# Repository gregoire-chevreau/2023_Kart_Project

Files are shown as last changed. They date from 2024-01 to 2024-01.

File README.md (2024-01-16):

# 2023_Kart_Project

Dans ce dossier GitHub, vous trouverez toutes les informations pour continuer le projet.
Ce dernier est composé d'une carte de commande avec la NUCLEO STM32G431RB ainsi que d'un onduleur.

## Table des matières

- [Cahier des charges](#charges)
- [PCB de commande](#commande)
- [Onduleur](#onduleur)
- [Code](#code)

## Cahier des charges

Le but est de faire rouler le kart à 20 km/h.
Le moteur est un moteur OZO 3500W à alimenter en 72 V (https://ozo-electric.com/fr/moteurs-centraux-brushless/679130-moteur-moto-3500w-electrique-central-brushless-bldc.html).
La batterie fourni une tension de  72V (https://ozo-electric.com/fr/72v/282892-batterie-72v-21ah-1512wh-pvc-panasonic-lithium.html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).

## PCB de commande

Ce PCB est composé de la carte NUCLEO, d'une isolation galvanique et d'un level-shifter.
L'isolation galvanique pourra disparaître pour faire un seul PCB commun par la suite. En effet, des optocoupleurs sont prévus comme driver de MOSFET.

## Onduleur

L'onduleur a les caractéristiques suivantes : 
- Tension d'alimentation : 72 V
- Courant nominal : 48 A
De plus, sur cette carte, nous avons prévu une alimentation 15V afin d'alimenter la carte de commande.

## Code

Le code est réalisé avec STM32CubeIDE.
Nous utilisons : 
- 6 sorties GPIO pour commander l’onduleur
- 3 entrées GPIO pour les capteurs Hall
- 1 entrée ADC pour le potentiomètre
- 1 entrée ADC pour le capteur de tension de la batterie
- 1 entrée ADC pour les capteurs de courant de phase

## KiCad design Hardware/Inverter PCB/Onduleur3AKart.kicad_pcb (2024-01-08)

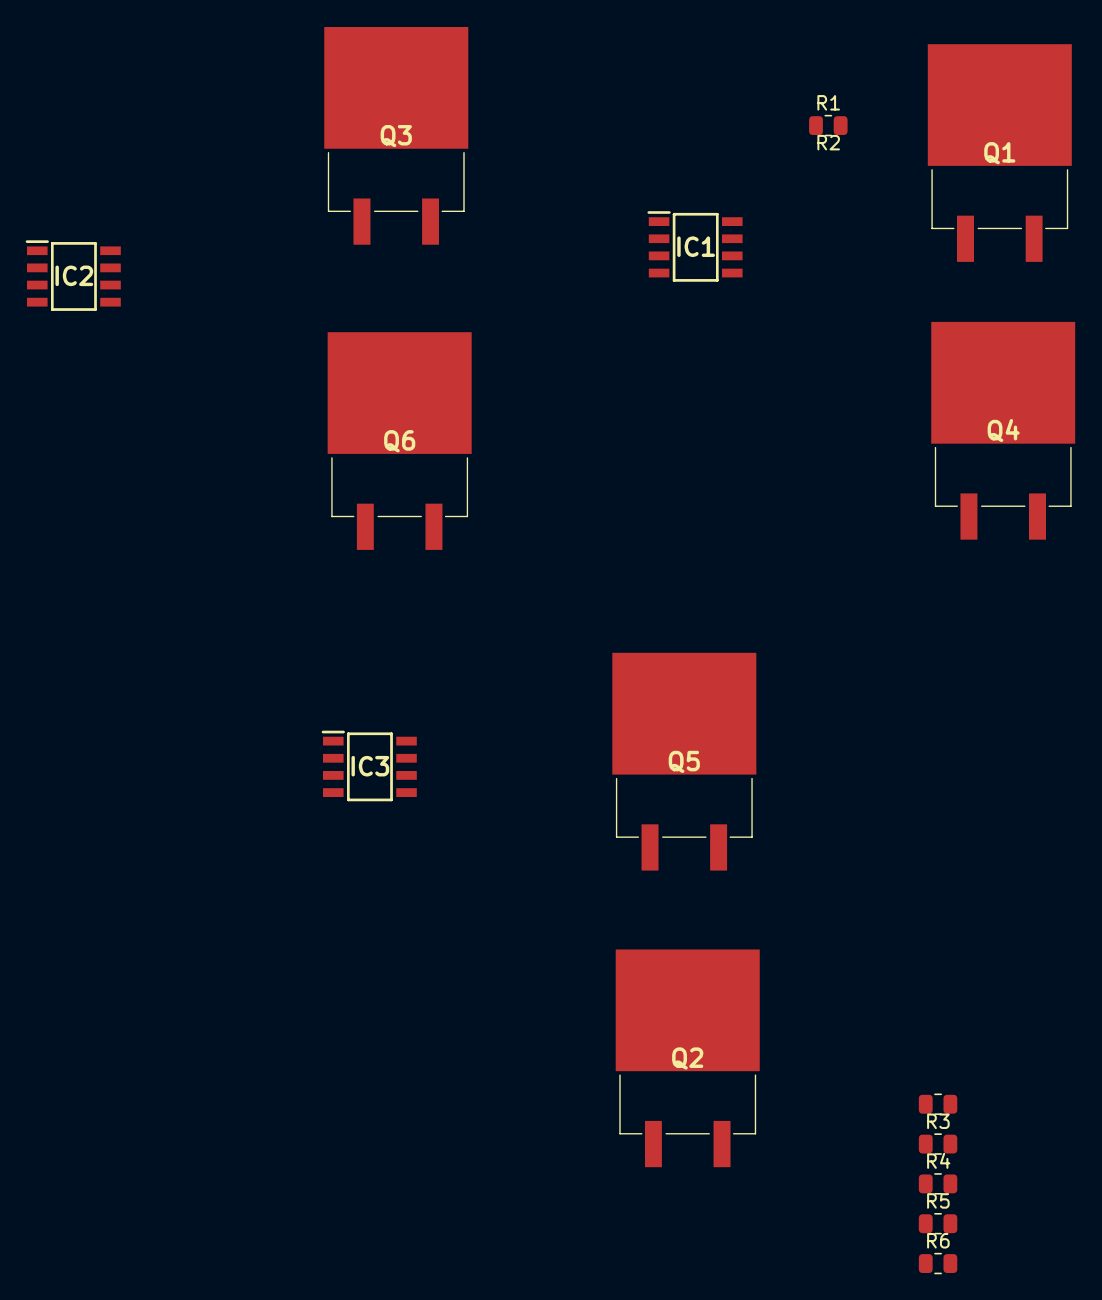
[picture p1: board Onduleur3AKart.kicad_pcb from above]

Board: 2 copper layers, 15 parts (0 on the bottom side), 15 nets, no tracks yet.

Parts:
IC1, IC2, IC3: TPS2836DR
Q1, Q2, Q3, Q4, Q5, Q6: SUM60N10-17-E3; SUM60N1017E3
R1, R3, R5: 1; R_0805_2012Metric
R2, R4, R6: 5; R_0805_2012Metric

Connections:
unnamed: IC1.6 (BOOTLO), R2.1
unnamed: IC1.7 (HIGHDR), R1.1
unnamed: IC2.6 (BOOTLO), R4.1
unnamed: IC2.7 (HIGHDR), R3.1
unnamed: IC3.6 (BOOTLO), R6.1
unnamed: IC3.7 (HIGHDR), R5.1
unnamed: Q1.1 (G), R1.2
unnamed: Q1.3 (S), Q4.2 (D)
unnamed: Q2.1 (G), R3.2
unnamed: Q2.3 (S), Q5.2 (D)
unnamed: Q3.1 (G), R5.2
unnamed: Q3.3 (S), Q6.2 (D)
unnamed: Q4.1 (G), R2.2
unnamed: Q5.1 (G), R4.2
unnamed: Q6.1 (G), R6.2

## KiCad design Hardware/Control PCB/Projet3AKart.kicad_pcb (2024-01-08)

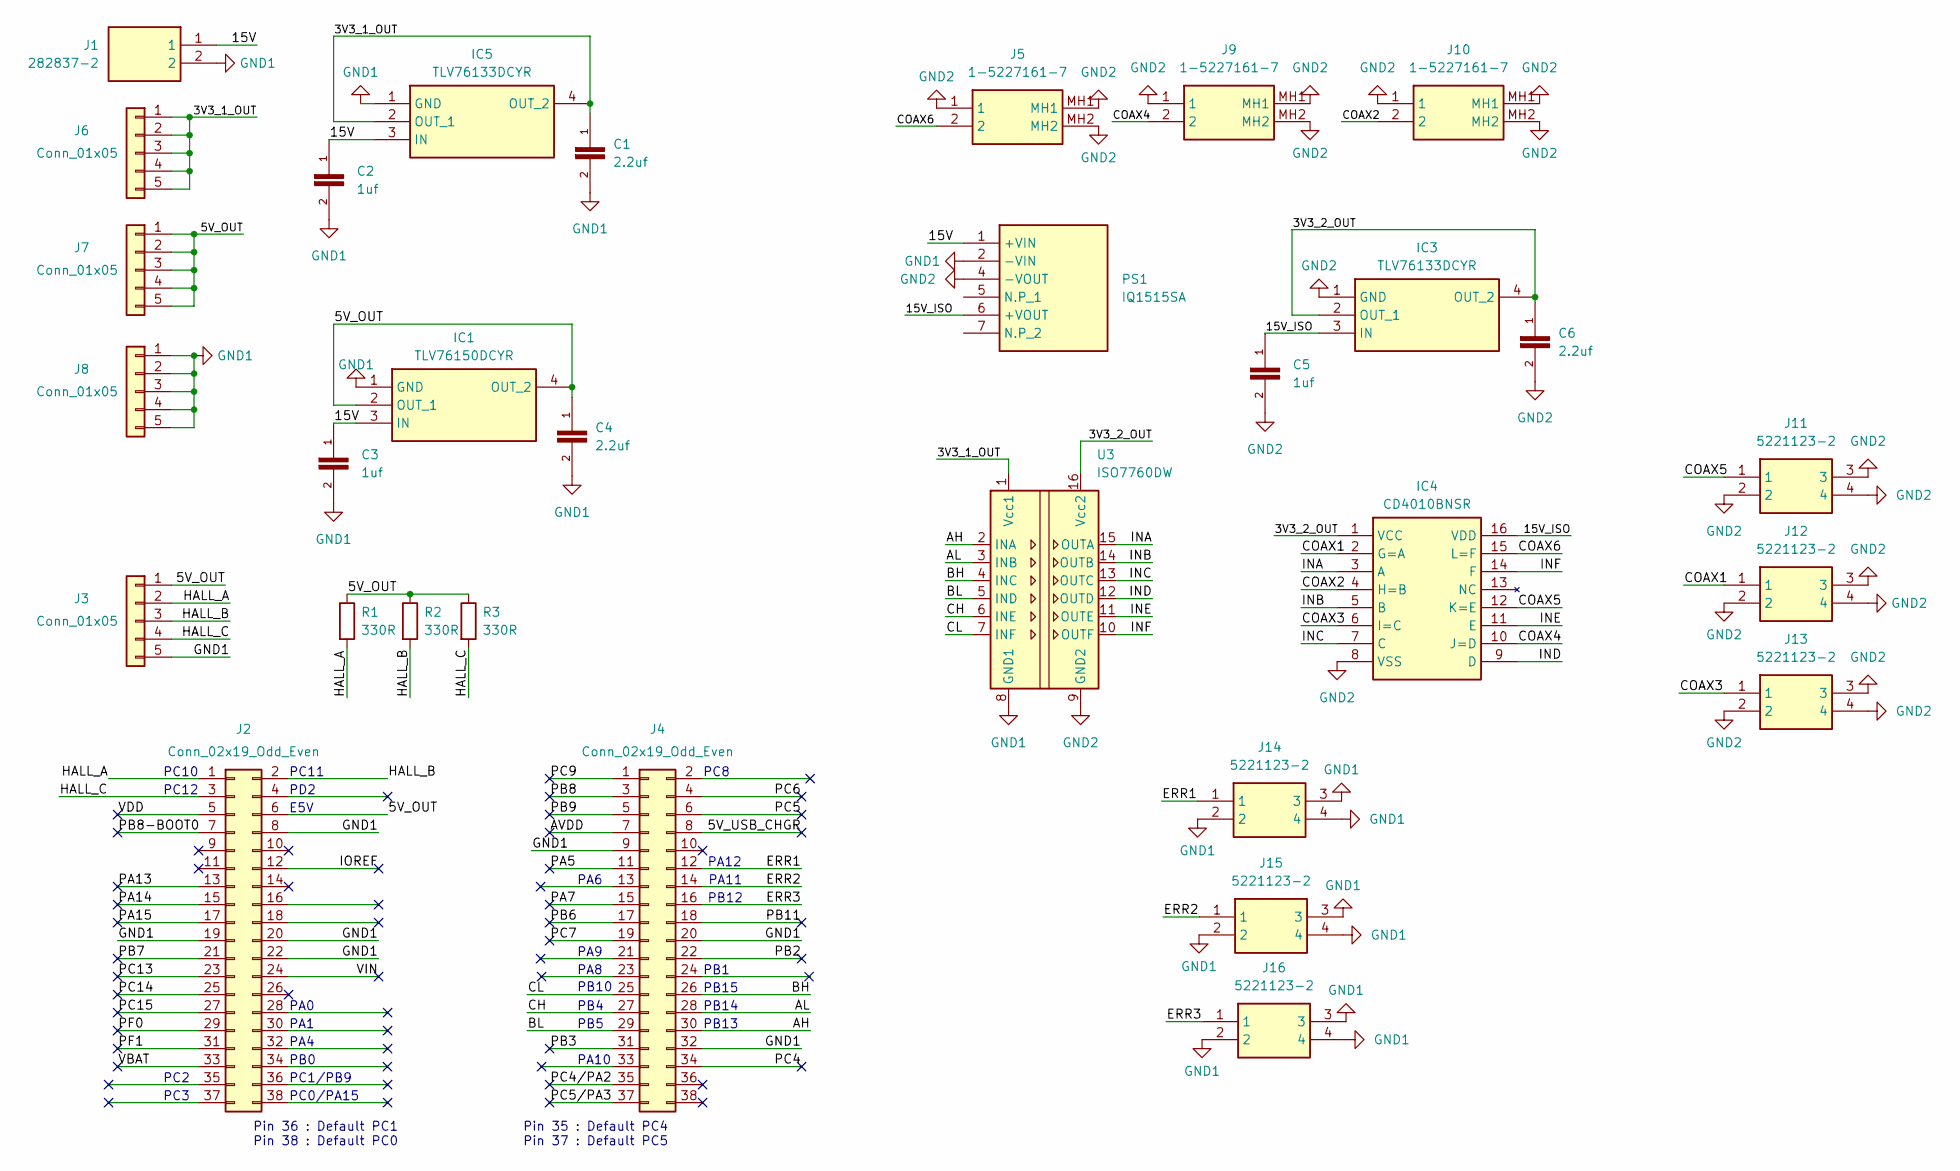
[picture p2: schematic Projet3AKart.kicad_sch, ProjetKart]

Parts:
C1, C4, C6: 2.2uf; CAPC2012X140N
C2, C3, C5: 1uf; CAPC2012X140N
IC1: TLV76150DCYR; Mouser Part Number 595-TLV76150DCYR
IC3, IC5: TLV76133DCYR; Mouser Part Number 595-TLV76133DCYR
IC4: CD4010BNSR; Mouser Part Number 595-CD4010BNSR
J1: 282837-2; 2828372; Mouser Part Number 571-2828372
J2, J4: Conn_02x19_Odd_Even; PinHeader_2x19_P2.54mm_Vertical
J3, J6, J7, J8: Conn_01x05; PinHeader_1x05_P2.54mm_Vertical
J5, J9, J10: 1-5227161-7; 152271617; Mouser Part Number 571-1-5227161-7
J11, J12, J13, J14, J15, J16: 5221123-2; 52211232; Manufacturer_Part_Number 5221123-2
PS1: IQ1515SA; Mouser Part Number 209-IQ1515SA
R1, R2, R3: 330R; R_0805_2012Metric
U3: ISO7760DW; SOIC-16W_7.5x10.3mm_P1.27mm

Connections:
/3V3_1_OUT: C1.1, IC5.2 (OUT_1), IC5.4 (OUT_2), J6.1, J6.2, J6.3, J6.4, J6.5, U3.1 (Vcc1)
/3V3_2_OUT: C6.1, IC3.2 (OUT_1), IC3.4 (OUT_2), IC4.1 (VCC), U3.16 (Vcc2)
/5V_OUT: C4.1, IC1.2 (OUT_1), IC1.4 (OUT_2), J2.6, J3.1, J7.1, J7.2, J7.3, J7.4, J7.5, R1.1, R2.1, R3.1
/5V_USB_CHGR: J4.8
/15V: C2.1, C3.1, IC1.3 (IN), IC5.3 (IN), J1.1, PS1.1 (+VIN)
/15V_ISO: C5.1, IC3.3 (IN), IC4.16 (VDD), PS1.6 (+VOUT)
/AH: J4.30, U3.2 (INA)
/AL: J4.28, U3.3 (INB)
/AVDD: J4.7
/BH: J4.26, U3.4 (INC)
/BL: J4.29, U3.5 (IND)
/CH: J4.27, U3.6 (INE)
/CL: J4.25, U3.7 (INF)
/COAX1: IC4.2 (G=A), J12.1
/COAX2: IC4.4 (H=B), J10.2
/COAX3: IC4.6 (I=C), J13.1
/COAX4: IC4.10 (J=D), J9.2
/COAX5: IC4.12 (K=E), J11.1
/COAX6: IC4.15 (L=F), J5.2
/ERR1: J4.12, J14.1
/ERR2: J4.14, J15.1
/ERR3: J4.16, J16.1
/HALL_A: J2.1, J3.2, R1.2
/HALL_B: J2.2, J3.3, R2.2
/HALL_C: J2.3, J3.4, R3.2
/INA: IC4.3 (A), U3.15 (OUTA)
/INB: IC4.5 (B), U3.14 (OUTB)
/INC: IC4.7 (C), U3.13 (OUTC)
/IND: IC4.9 (D), U3.12 (OUTD)
/INE: IC4.11 (E), U3.11 (OUTE)
/INF: IC4.14 (F), U3.10 (OUTF)
/IOREF: J2.12
/PA5: J4.11
/PA7: J4.15
/PA13: J2.13
/PA14: J2.15
/PA15: J2.17
/PB2: J4.22
/PB3: J4.31
/PB6: J4.17
/PB7: J2.21
/PB8: J4.3
/PB8-BOOT0: J2.7
/PB9: J4.5
/PB11: J4.18
/PC4: J4.34
/PC4/PA2: J4.35
/PC5: J4.6
/PC5/PA3: J4.37
/PC6: J4.4
/PC7: J4.19
/PC9: J4.1
/PC13: J2.23
/PC14: J2.25
/PC15: J2.27
/PF0: J2.29
/PF1: J2.31
/VBAT: J2.33
/VDD: J2.5
/VIN: J2.24
GND1: C1.2, C2.2, C3.2, C4.2, IC1.1 (GND), IC5.1 (GND), J1.2, J2.8, J2.19, J2.20, J2.22, J3.5, J4.9, J4.20, J4.32, J8.1, J8.2, J8.3, J8.4, J8.5, J14.2, J14.3, J14.4, J15.2, J15.3, J15.4, J16.2, J16.3, J16.4, PS1.2 (-VIN), U3.8 (GND1)
GND2: C5.2, C6.2, IC3.1 (GND), IC4.8 (VSS), J5.1, J5.MH1, J5.MH2, J9.1, J9.MH1, J9.MH2, J10.1, J10.MH1, J10.MH2, J11.2, J11.3, J11.4, J12.2, J12.3, J12.4, J13.2, J13.3, J13.4, PS1.4 (-VOUT), U3.9 (GND2)

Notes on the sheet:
PB14
PA11
PA8
PB12
PC2
PB5
PA9
PC11
PC12
E5V
PB1
PA4
PB13
PC1/PB9
PB4
PA10
PD2
PC8
PB10
PA6
PB15
PC3
PC10
PA0
PA1
PA12
PB0
Pin 35 : Default PC4 Pin 37 : Default PC5
PC0/PA15
Pin 36 : Default PC1 Pin 38 : Default PC0

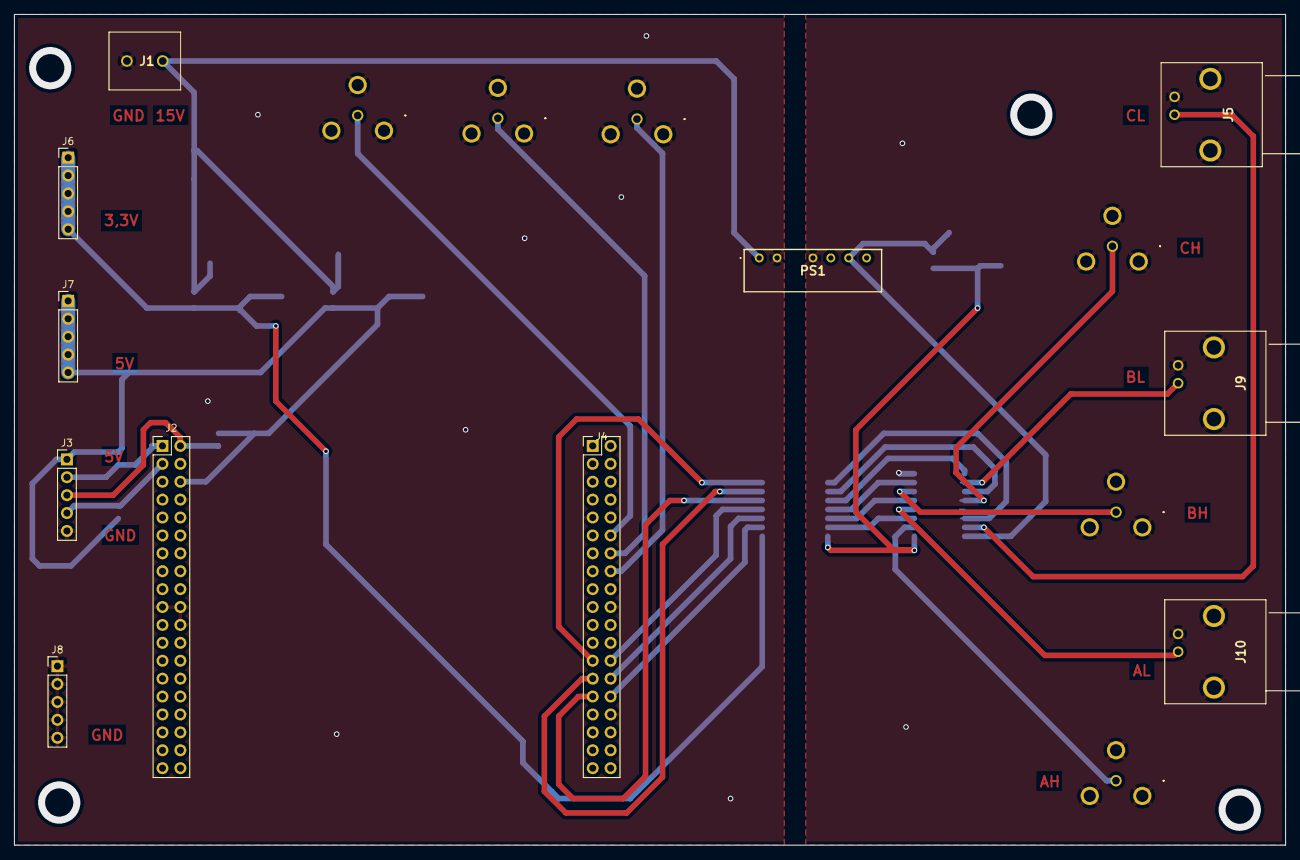
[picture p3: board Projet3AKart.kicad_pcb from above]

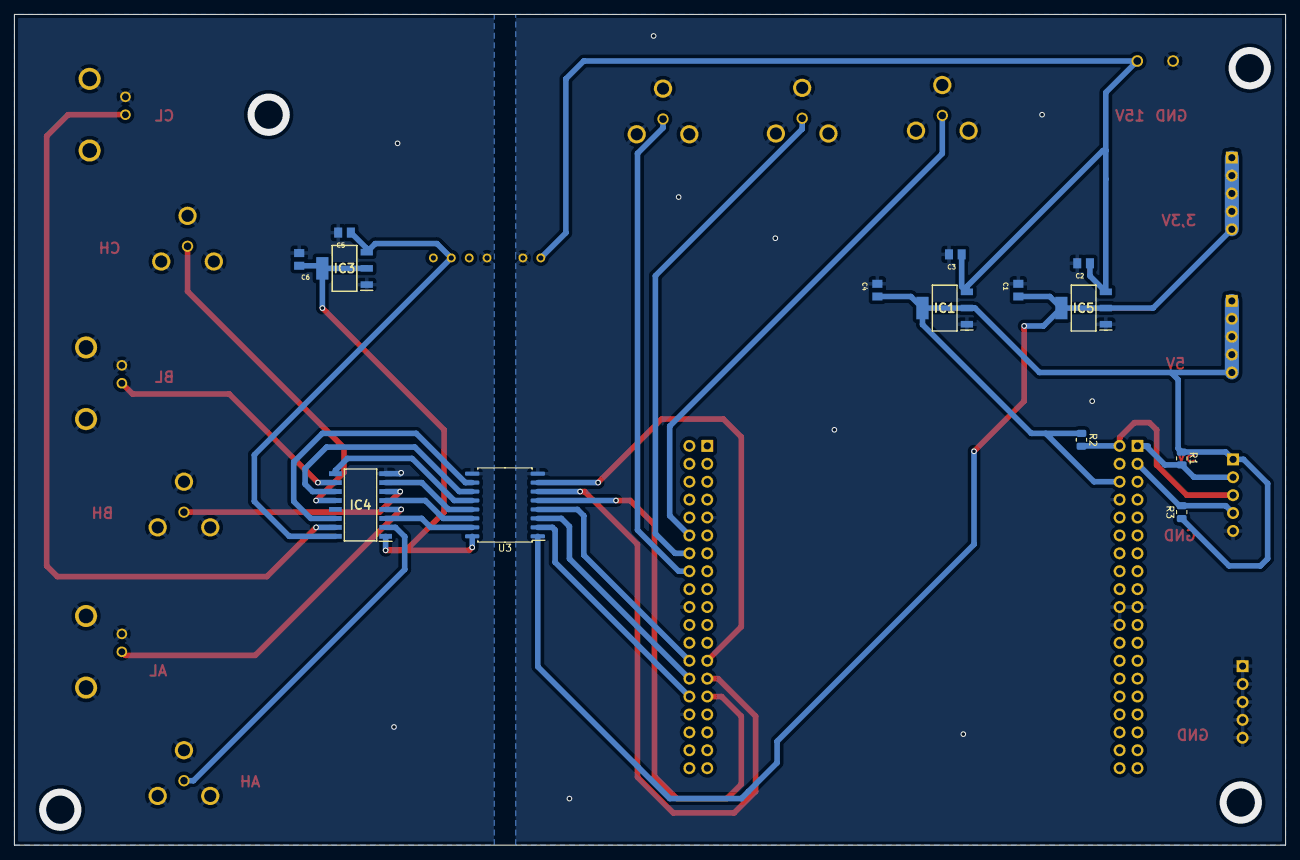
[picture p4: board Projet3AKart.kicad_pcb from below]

Board: 2 copper layers, 180.3 x 117.9 mm, 31 parts (14 on the bottom side), 31 nets.

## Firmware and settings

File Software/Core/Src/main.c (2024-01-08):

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
/* Includes ------------------------------------------------------------------*/
#include "main.h"
#include "adc.h"
#include "usart.h"
#include "tim.h"
#include "gpio.h"

/* USER CODE BEGIN Includes */
#include "stm32g4xx_hal.h"
#include "math.h"
/* USER CODE END Includes */


void SystemClock_Config(void);
/* USER CODE BEGIN PFP */
void MX_GPIO_Init(void);
void Error_Handler(void);
/* USER CODE END PFP */

/* USER CODE BEGIN 0 */
uint8_t Hall_A;
uint8_t Hall_B;
uint8_t Hall_C;
/* USER CODE END 0 */

/**
  * @brief  The application entry point.
  * @retval int
  */
int main(void)
{
  /* MCU Configuration--------------------------------------------------------*/

  /* Reset of all peripherals, Initializes the Flash interface and the Systick. */
  HAL_Init();

  /* Configure the system clock */
  SystemClock_Config();

  /* Initialize all configured peripherals */
  MX_GPIO_Init();
  MX_LPUART1_UART_Init();
  MX_TIM1_Init();
  MX_ADC1_Init();
  /* USER CODE BEGIN 2 */

  int value = 0;

  /* USER CODE END 2 */

  /* Infinite loop */
  /* USER CODE BEGIN WHILE */
  while (1)
  {
	  Hall_A = HAL_GPIO_ReadPin(GPIOC, GPIO_PIN_10);
	  Hall_B = HAL_GPIO_ReadPin(GPIOC, GPIO_PIN_11);
	  Hall_C = HAL_GPIO_ReadPin(GPIOC, GPIO_PIN_12);

	  //value = adc_value();
	  value = 1000;
	  PWM(Hall_A, Hall_B, Hall_C);
	  HAL_Delay(value);

	  error;
    /* USER CODE END WHILE */

    /* USER CODE BEGIN 3 */
  }
  /* USER CODE END 3 */
}

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


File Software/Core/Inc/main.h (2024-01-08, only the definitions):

#define B1_Pin GPIO_PIN_13
#define B1_GPIO_Port GPIOC
#define LPUART1_TX_Pin GPIO_PIN_2
#define LPUART1_TX_GPIO_Port GPIOA
#define LPUART1_RX_Pin GPIO_PIN_3
#define LPUART1_RX_GPIO_Port GPIOA
#define LD2_Pin GPIO_PIN_5
#define LD2_GPIO_Port GPIOA
#define T_SWDIO_Pin GPIO_PIN_13
#define T_SWDIO_GPIO_Port GPIOA
#define T_SWCLK_Pin GPIO_PIN_14
#define T_SWCLK_GPIO_Port GPIOA
#define T_SWO_Pin GPIO_PIN_3
#define T_SWO_GPIO_Port GPIOB

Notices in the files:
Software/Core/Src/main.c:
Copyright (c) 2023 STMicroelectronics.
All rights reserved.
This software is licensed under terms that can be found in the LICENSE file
